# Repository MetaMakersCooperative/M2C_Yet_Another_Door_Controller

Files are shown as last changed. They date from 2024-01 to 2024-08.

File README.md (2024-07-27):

# M2C Yet Another Door Controller

Proof of concept for new door controller design using a `WT32-ETH01`.

## Development Requirements

Make sure version `v1.X` of the Arduino IDE installed. It is required to upload the cards file. See [Cards File](#cards_file) section.

`arduino-cli` also needs to be installed to compile and upload the sketch. It is possible to use the Arduino IDE `v1.X` or `v2` but they have not been tested/verified. Milage may vary.

## Cards File

The sketch assumes a file named `cards.txt` exists within a `LitteFS` file system. The code will not function correctly without it.

Unfortunately, the only way to upload the file to the device is using `v1.X` Arduino IDE. This is because the upload using a plugin that only can be used with that version of the IDE. Setting up the upload plugin is only required if the `cards.txt` file needs to be updated or if the flash storage was wiped.

### Setup the Upload Plugin

To setup the plugin, follow the steps outlined below:

1. First download the following `zip` file: [https://github.com/lorol/arduino-esp32fs-plugin/releases/download/2.0.7/esp32fs.zip](https://github.com/lorol/arduino-esp32fs-plugin/releases/download/2.0.7/esp32fs.zip)
2. Unzip and place the `esp32fs.jar` file in the following directory: `~/Arduino/tools/ESP32FS/tool/esp32fs.jar`
3. Restart Arduino IDE if it's running

### Uploading

Before uploading, create the `data` directory in the project root if it does not already exist. Update/create the `card.txt` file with the codes that should unlock the door. Make sure each code is in it's own line, like below:

> Each code should be no more than 10 digits long and only container digits `0-9`. No leading zeros!

```text
1234567
8912345
6789123
```

Double check and make sure the project structure matches the following:

```text
~/Arduino/M2C_Yet_Another_Door_Controller/
├── data
│   └── cards.txt
├── README.md
├── sketch.yaml
└── M2C_Yet_Another_Door_Controller.ino
```

To upload the `card.txt` file, follow the steps outlined below:

> When referencing the Arduino IDE, it is implied that it's `v1.X` not `v2`

1. Open Arduino IDE and open the `M2CYetAnotherDoorController.ino` sketch.
2. Navigate and click on `Tools -> Board` and select `WT32-ETH01 Ethernet Module` if it is not already selected.
3. Navigate and click on `Tools -> ESP32 Sketch Date Upload`
4. Select `LittleFS` then click `OK`

## Libraries

To install the `esp32` libraries run the following command:

```bash
arduino-cli core install esp32:esp32@3.0.2
```

> Might need to run `arduino-cli core update-index` to update the board index.

This will install [espressif/arduino-esp32 version `3.0.2`](https://github.com/espressif/arduino-esp32/tree/3.0.2).

The following libraries can be installed using the Arduino IDE or by downloading the files directly from the source repositories.

When downloading the libraries manually, make sure the source is place them within the following directory: `~/Arduino/libraries`.

The `libraries` should look like this assuming the only installed libraries are the ones used by this project.

```
~/Arduino/libraries
├── LinkedList
│   ├── ...
└── Yet_Another_Arduino_Wiegand_Library
    ├── ...
```

> Make sure to download the source tagged with the versions listed below!

The following dependencies need to be installed manually as the latest versions are required:

> The best way to get these libraries is to `git clone` them into the `~/Arduino/libraries` directory.

- [Yet Another Arduino Wiegand Library](https://github.com/paulo-raca/YetAnotherArduinoWiegandLibrary) commit: `556e7b8` tag: `2.0.1`
- [LinkedList](https://github.com/ivanseidel/LinkedList) commit: `0439a72` tag: `v1.3.3`
- [espMqttClient](https://github.com/bertmelis/espMqttClient) commit: `70d3113` tag: `v1.7.0`
- [AsyncTCP](https://github.com/mathieucarbou/AsyncTCP) commit: `b20e92e` tag: `v3.1.4`

> AsyncTCP is still required even though it's not being used

## Commands (using CLI)

> Note: `/dev/ttyUSB0` is the default device. Run the following command to see what device is being used: `arduino-cli board list`. Make sure to modify the commands below to match that device.

To compile the sketch with defaults, run following command:

> WARNING: Defaults will apply not overridden which could cause a lot of problems on multi door deployments. See the [Override Defaults](#override-defaults) section below.

```bash
arduino-cli compile --fqbn esp32:esp32:wt32-eth01 ./
```

To enable more debugging messages, run the following command:

```bash
arduino-cli compile --build-property "build.extra_flags=\"-DDC_DEBUG=1\"" --clean --fqbn esp32:esp32:wt32-eth01 ./
```

To Upload the compiled sketch:

```bash
arduino-cli upload -p /dev/ttyUSB0 --fqbn esp32:esp32:wt32-eth01 ./
```

To monitor the serial output:

```bash
arduino-cli monitor --log-level debug --fqbn esp32:esp32:wt32-eth01 -p /dev/ttyUSB0 -c baudrate=115200
```
## MQTT Broker

> NOTE: The code assumes the MQTT server connection is TLS. Only TLS v1.2 is supported. Using TLS v1.3 will result in some weird errors. 

The device will send logs, lock, unlock, and other events to the configured MQTT broker. If disconnected, only a few messages will be queued and sent when it's able to reconnect.

If the `door_controller/access_list` topic is received, the device will replace the card file with the payload, then attempt to reload the list from the updated file.

The device will also respond to messages with the `door_controller/health_check` topic. This is designed to help with monitoring the healthiness of the device.

### `root_ca.h`

Use the example file, `root_ca.h.example`, to create the `root_ca.h` file containing the root certificate for the MQTT broker.

> NOTE: The root certificate will expire at some point so make sure you mark it in your calendar!

If you're using Let's Encrypt, then there is a good chance that the root certificate can be download from the following URL: [letsencrypt.org/certs/isrgrootx1.pem](https://letsencrypt.org/certs/isrgrootx1.pem)

Otherwise, check out [letsencrypt.org/certificates/](https://letsencrypt.org/certificates/) for a complete list.

## Override Defaults

> Note: Make sure the latest Arduino CLI is installed

The table below shows the build flags that should be overridden for each controller being deployed.
Refer to the source files for a complete list of overridable flags.

| Flag Name | Default | Description | Build Argument |
|---|---|---|---|
| DC_HOST_NAME | m2cdoorone | The value that will be set as the device's host name | -DDC_HOST_NAME=m2cdoorone |
| DC_CLIENT_ID | door_one | Client ID is used by the MQTT broker to identify the client. This value needs to be unique across all clients connected to the broker | -DDC_CLIENT_ID=door_one |
| DC_MQTT_HOST | mqtt.metamakers.org | Host name for the MQTT Broker. The host name is used to get the server IP using DNS | -DDC_MQTT_HOST=mqtt.metamakers.org |
| DC_MQTT_USER | door_one | The user that the MQTT client will use to authenticate | -DDC_MQTT_USER=door_one |
| DC_MQTT_PW | Door_One!1 | The password that the MQTT client will use to authenticate | -DDC_MQTT_PW=Door_One!1 |
| DC_NTP_HOST  | pool.ntp.org | The domain used to update the RTC using NTP | -DDC_NTP_HOST=pool.ntp.org |
| DC_DEBUG | 0 | Enable more verbose debugging information via the serial port. Do not enable this for production deployments | -DDC_DEBUG=0 |

Below is an example of how to override all the flags in the table above:

> Documentation on the CLI compile command can be found [here](https://arduino.github.io/arduino-cli/1.0/commands/arduino-cli_compile/).

```bash
arduino-cli compile --build-property "build.extra_flags=-DDC_DEBUG=0 \"-DDC_HOST_NAME=\"m2cdoorone\"\" \"-DDC_CLIENT_ID=\"door_one\"\" \"-DDC_MQTT_HOST=\"mqtt.metamakers.org\"\" \"-DDC_MQTT_USER=\"door_one\"\" \"-DDC_MQTT_PW=\"Door_One!1\"\" \"-DDC_NTP_HOST=\"pool.ntp.org\"\"" --clean --fqbn esp32:esp32:wt32-eth01 ./
```

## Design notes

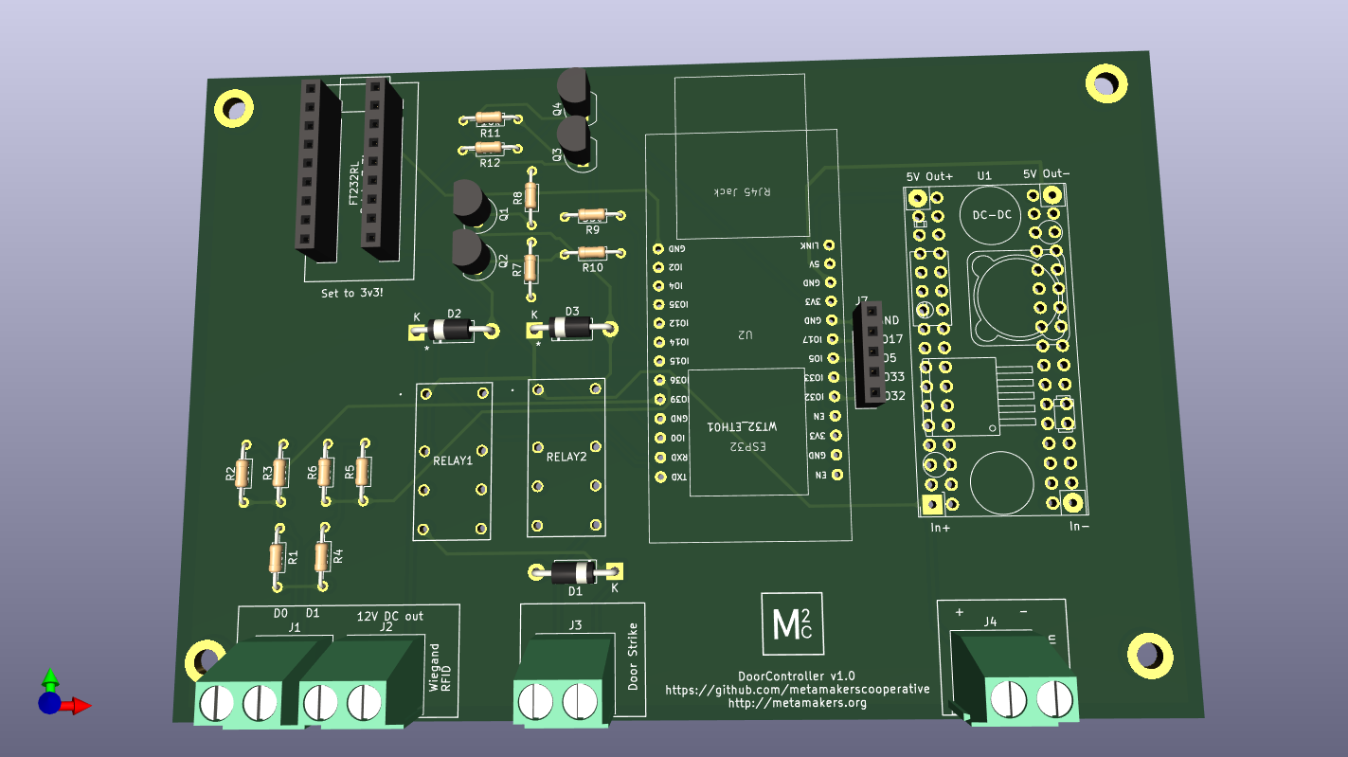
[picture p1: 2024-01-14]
PCB/door-controller.png

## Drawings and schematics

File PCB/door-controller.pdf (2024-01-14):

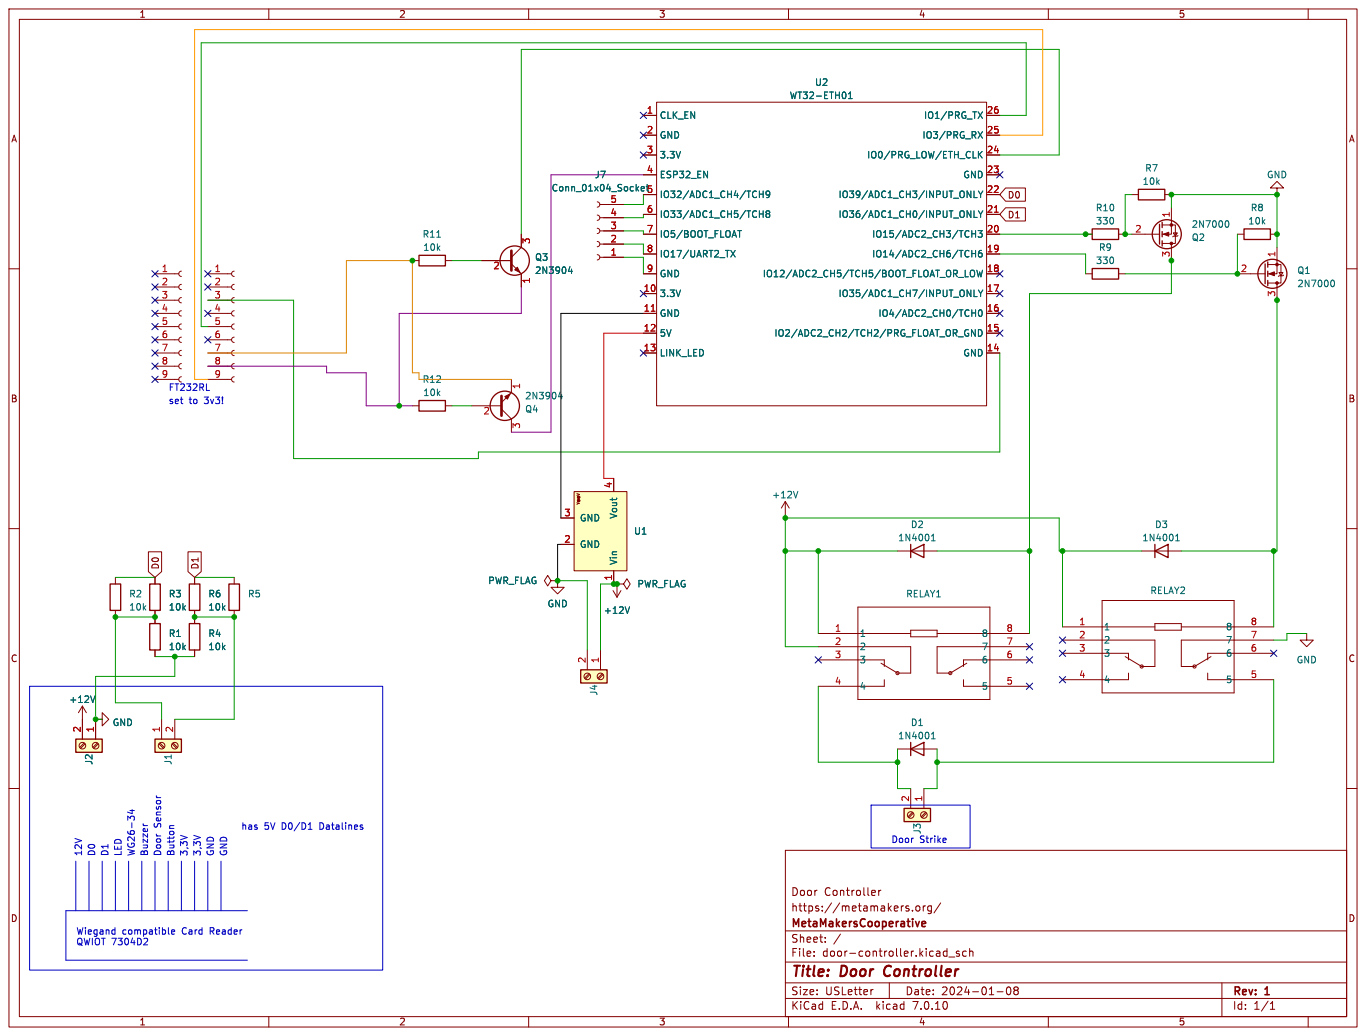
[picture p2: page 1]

1 GND 2 GND 3 Vout 4 U1
https://metamakers.org/ Door Controller 1

Id: 1/1 Title: Door Controller File: door-controller.kicad_sch Sheet: / MetaMakersCooperative

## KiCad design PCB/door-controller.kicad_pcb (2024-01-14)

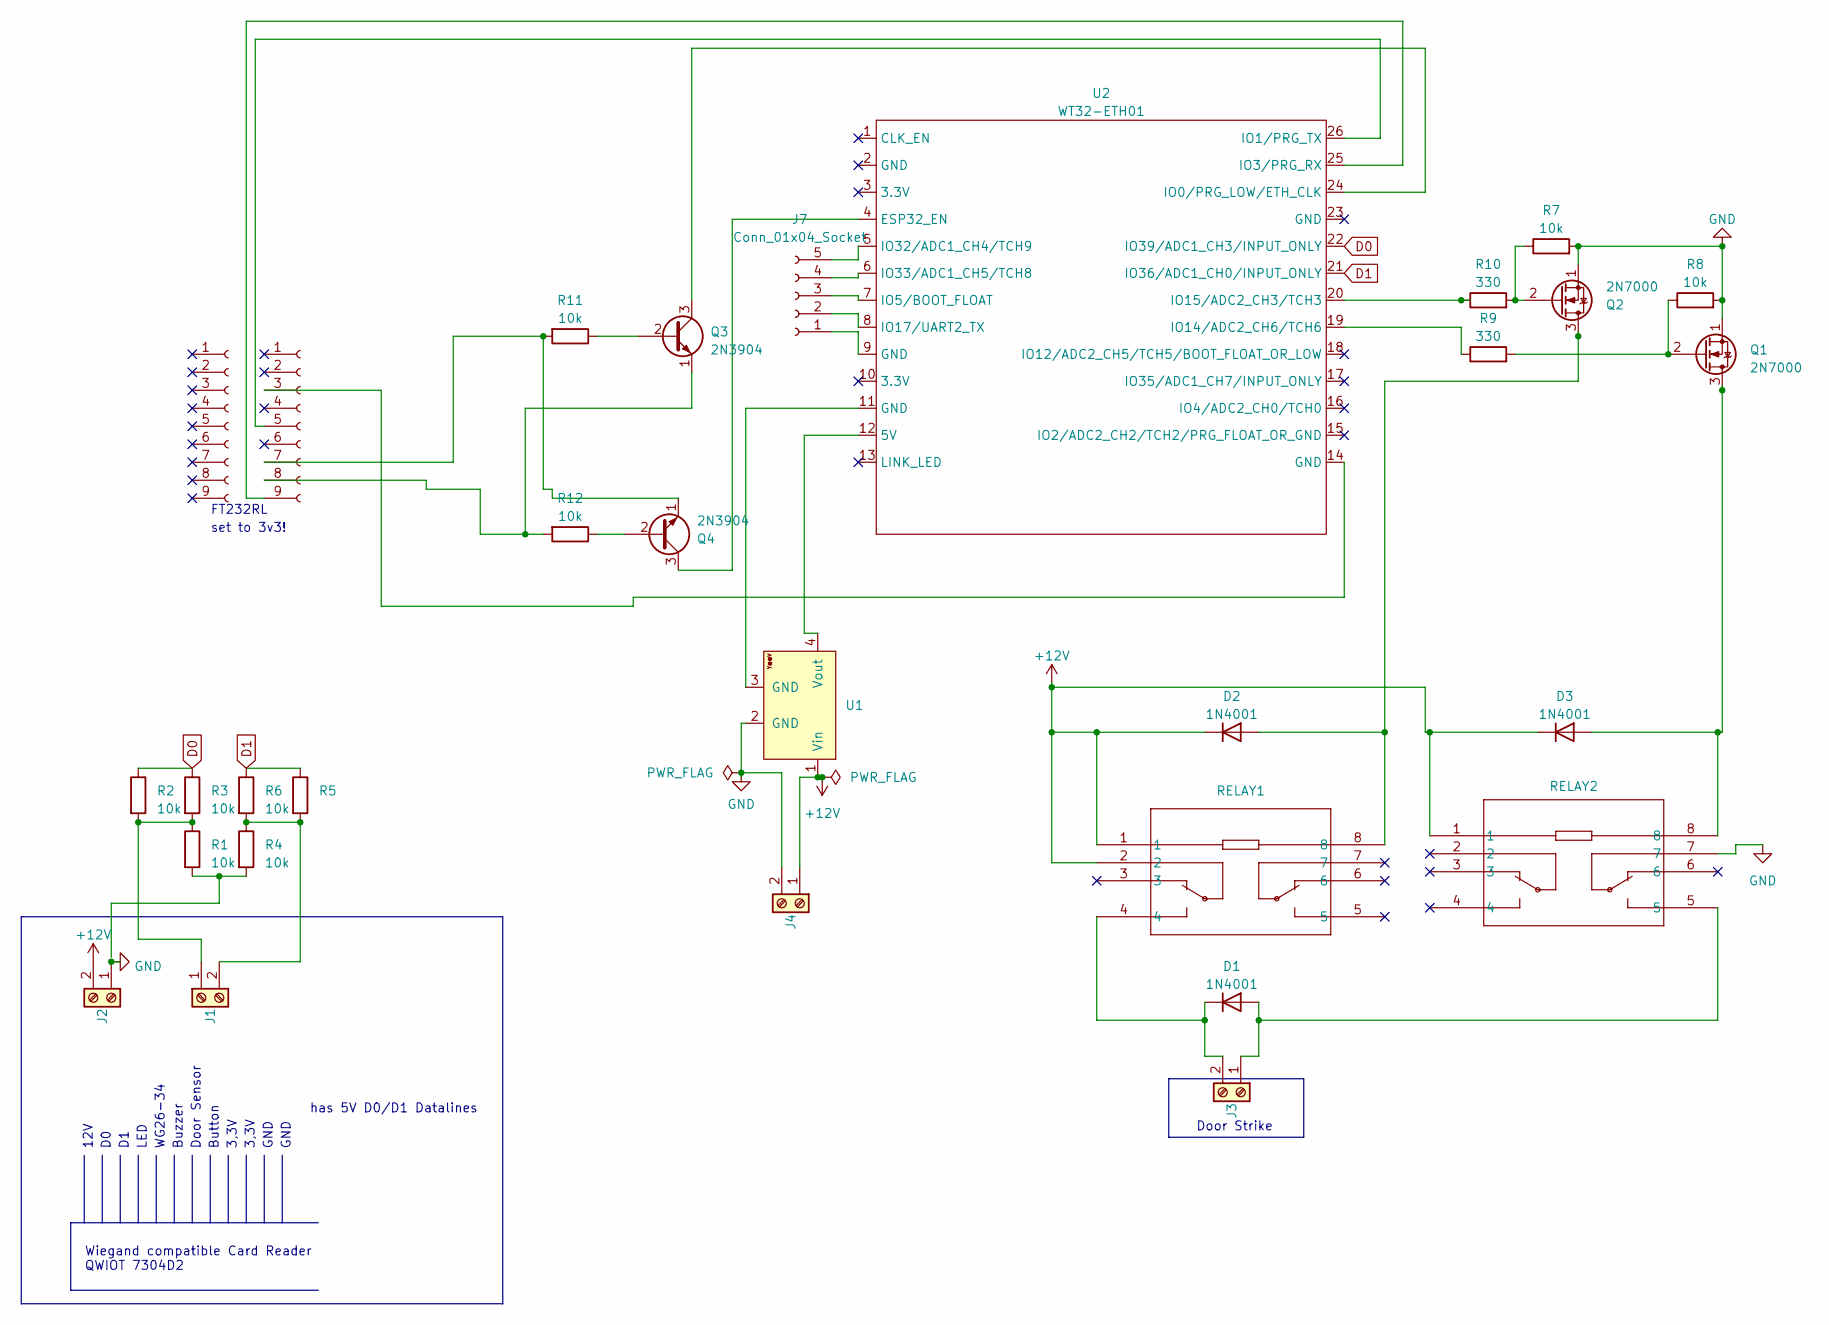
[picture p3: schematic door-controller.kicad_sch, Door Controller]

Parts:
D1, D2, D3: 1N4001; D_DO-41_SOD81_P10.16mm_Horizontal
J1, J2, J3, J4: TerminalBlock_Phoenix_MKDS-1,5-2_1x02_P5.00mm_Horizontal
J5, J6: Conn_01x09_Socket; PinSocket_1x09_P2.54mm_Vertical
J7: Conn_01x04_Socket; PinSocket_1x05_P2.54mm_Vertical
Q1, Q2: 2N7000; TO-92_Inline
Q3, Q4: 2N3904; TO-92_Inline
R1, R2, R3, R4, R5, R6, R7, R8, R11, R12: 10k; R_Axial_DIN0204_L3.6mm_D1.6mm_P7.62mm_Horizontal
R9, R10: 330; R_Axial_DIN0204_L3.6mm_D1.6mm_P7.62mm_Horizontal
RELAY1, RELAY2: RELAY8_J104D2C12VDC.20S_CRS
U1: YAAJ_DCDC_StepDown_LM2596; YAAJ_DCDC_StepDown_LM2596_Universal
U2: WT32-ETH01

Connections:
+12V: D2.1 (K), D3.1 (K), J2.2, J4.1, RELAY1.1, RELAY1.2, RELAY2.1, U1.1 (Vin)
D0: R2.1, R3.1, U2.22 (IO39/ADC1_CH3/INPUT_ONLY)
D1: R5.1, R6.1, U2.21 (IO36/ADC1_CH0/INPUT_ONLY)
GND: J2.1, J4.2, Q1.1 (S), Q2.1 (S), R7.2, R8.2, RELAY2.7, U1.2 (GND)
unnamed: D1.2 (A), J3.1, RELAY2.5
unnamed: D1.1 (K), J3.2, RELAY1.4
unnamed: D2.2 (A), Q2.3 (D), RELAY1.8
unnamed: D3.2 (A), Q1.3 (D), RELAY2.8
unnamed: J1.1, R1.1, R2.2, R3.2
unnamed: J1.2, R4.1, R5.2, R6.2
unnamed: J6.3, U2.14 (GND)
unnamed: J6.5, U2.26 (IO1/PRG_TX)
unnamed: J6.7, Q4.1 (E), R11.2
unnamed: J6.8, Q3.1 (E), R12.2
unnamed: J6.9, U2.25 (IO3/PRG_RX)
unnamed: J7.1, U2.9 (GND)
unnamed: J7.2, U2.8 (IO17/UART2_TX)
unnamed: J7.3, U2.7 (IO5/BOOT_FLOAT)
unnamed: J7.4, U2.6 (IO33/ADC1_CH5/TCH8)
unnamed: J7.5, U2.5 (IO32/ADC1_CH4/TCH9)
unnamed: Q1.2 (G), R8.1, R9.2
unnamed: Q2.2 (G), R7.1, R10.2
unnamed: Q3.2 (B), R11.1
unnamed: Q3.3 (C), U2.24 (IO0/PRG_LOW/ETH_CLK)
unnamed: Q4.2 (B), R12.1
unnamed: Q4.3 (C), U2.4 (ESP32_EN)
unnamed: R1.2, R4.2
unnamed: U1.3 (GND), U2.11 (GND)
unnamed: U1.4 (Vout), U2.12 (5V)
unnamed: R9.1, U2.19 (IO14/ADC2_CH6/TCH6)
unnamed: R10.1, U2.20 (IO15/ADC2_CH3/TCH3)

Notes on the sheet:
12V
3,3V
Door Strike
Buzzer
WG26-34
Button
GND
FT232RL
has 5V D0/D1 Datalines
Wiegand compatible Card Reader QWIOT 7304D2
Door Sensor
LED
GND
set to 3v3!

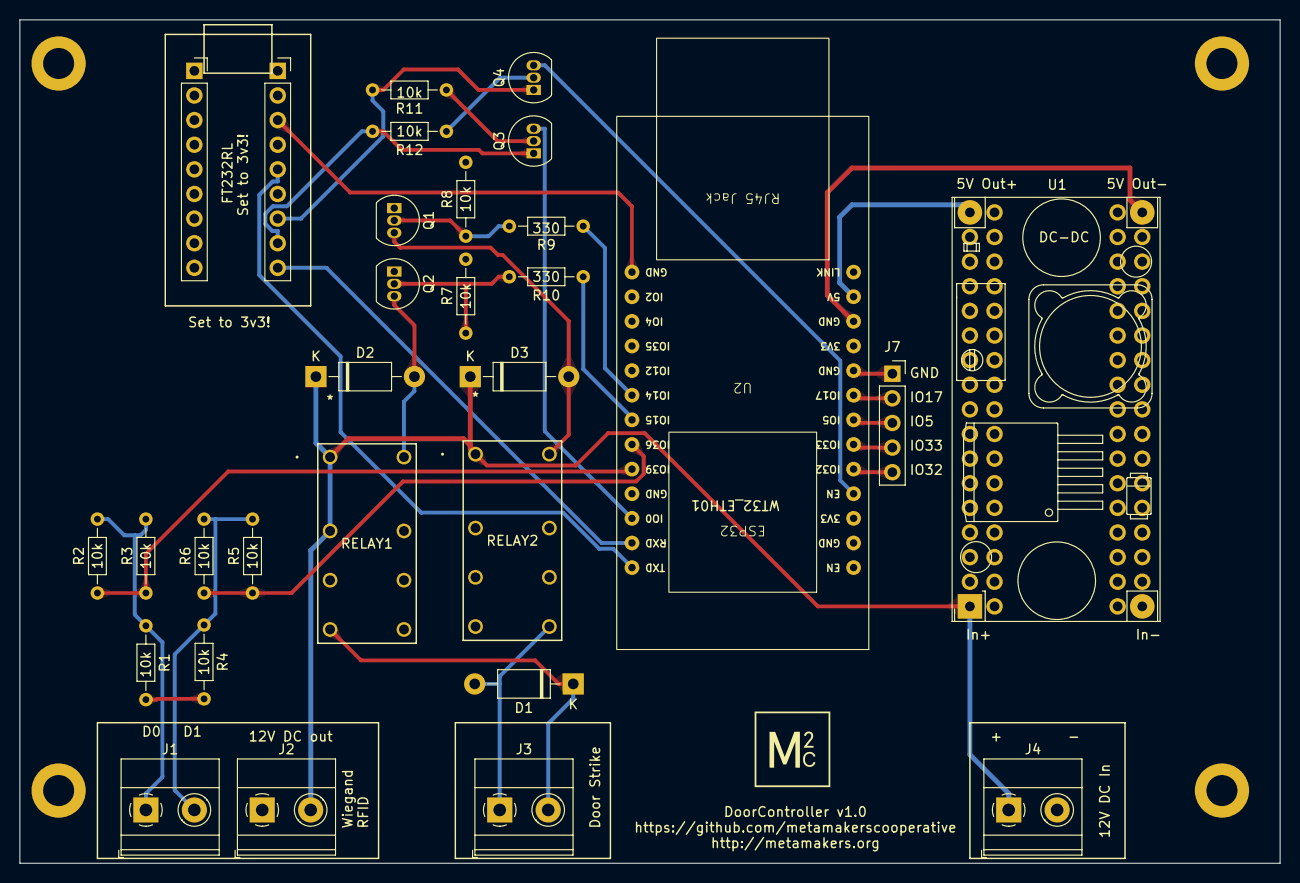
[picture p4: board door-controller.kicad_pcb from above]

Board: 2 copper layers, 130.0 x 87.0 mm, 34 parts (0 on the bottom side), 31 nets.

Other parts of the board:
MH1, MH2, MH3, MH4: MountingHole_3.2mm_M3_DIN965_Pad

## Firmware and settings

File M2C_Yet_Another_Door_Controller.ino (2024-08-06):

#include <Wiegand.h>
#include <LittleFS.h>
#include <LinkedList.h>
#include <errno.h>
// Dependencies: freertos/FreeRTOS.h and AsyncTCP.h
#include <espMqttClient.h>

// Note: These need to be defined BEFORE including ETH.h or calling ETH.begin()
#ifndef ETH_PHY_TYPE
#define ETH_PHY_TYPE ETH_PHY_LAN8720
#define ETH_PHY_ADDR 0
#define ETH_PHY_MDC 23
#define ETH_PHY_MDIO 18
#define ETH_PHY_POWER -1
#define ETH_CLK_MODE ETH_CLOCK_GPIO0_IN
#endif

#include <ETH.h>

#include "root_ca.h"

// The value that will be set as the device's host name
#ifndef DC_HOST_NAME
#define DC_HOST_NAME "m2cdoorone"
#endif

// Client ID is used by the MQTT broker to identify the client
// This value needs to be unique across all clients connected to the broker
#ifndef DC_CLIENT_ID
#define DC_CLIENT_ID "door_one"
#endif

// Host name for the MQTT Broker. The host name is used to get the server IP using DNS
#ifndef DC_MQTT_HOST
#define DC_MQTT_HOST "mqtt.metamakers.org"
#endif

// The user that the MQTT client will use to authenticate
#ifndef DC_MQTT_USER
#define DC_MQTT_USER "door_one"
#endif

// The password that the MQTT client will use to authenticate
#ifndef DC_MQTT_PW
#define DC_MQTT_PW "Door_One!1"
#endif

// The domain used to update the RTC using NTP
#ifndef DC_NTP_HOST
#define DC_NTP_HOST "pool.ntp.org"
#endif

// Enable more verbose debugging information via the serial port
// Do not enable this for production deployments
#ifndef DC_DEBUG
#define DC_DEBUG 0
#endif

// How long the client should wait before trying to reconnect to the MQTT Broker
#define DC_MQTT_RECONNECT_DELAY 20000

// How long to wait to refresh the RTC using NTP
// Default is set to 1 day
#define DC_NTP_REFRESH_TIME 86400000

// Publish MQTT topics with the client ID as the last level
#define TOPIC_LOG_INFO "door_controller/log_info/" DC_CLIENT_ID
#define TOPIC_LOG_WARN "door_controller/log_warn/" DC_CLIENT_ID
#define TOPIC_LOG_FATAL "door_controller/log_fatal/" DC_CLIENT_ID
#define TOPIC_UNLOCK "door_controller/unlock/" DC_CLIENT_ID
#define TOPIC_LOCK "door_controller/lock/" DC_CLIENT_ID
#define TOPIC_DENIED_ACCESS "door_controller/denied_access/" DC_CLIENT_ID
#define TOPIC_CHECK_IN "door_controller/check_in/" DC_CLIENT_ID

// Subscribe MQTT topics
#define TOPIC_ACCESS_LIST "door_controller/access_list"
#define TOPIC_HEALTH_CHECK "door_controller/health_check"

// These are the pins connected to the Wiegand D0 and D1 signals.
// Ensure your board supports external Interruptions on these pins
#define PIN_D0 39
#define PIN_D1 36

// Change this value to increase/decrease the amount of time the
// door is unlocked
#define UNLOCK_DOOR_MS 8000

// Relay pins to (un)lock the door
#define PIN_IO14 15
#define PIN_IO15 14

// Possible door states
#define STATE_NORMAL 0
#define STATE_UNLOCKED 1
#define STATE_COMPARING 2
#define STATE_MATCH 3

struct DoorState {
    uint8_t state;
    uint32_t cardCode;
    long doorUnlockedAtMS;
    int cursor;
};

espMqttClientSecure mqttClient(espMqttClientTypes::UseInternalTask::NO);
static TaskHandle_t taskHandle;

long lastReconnectAttempt = 0;

LinkedList<uint32_t> codeList = LinkedList<uint32_t>();

Wiegand wiegand;

DoorState doorState;

IPAddress mqttServerIp;
bool hasIp = false;

long lastNTPRefresh = 0;

void setup() {
    Serial.begin(115200);
    Serial.println("Listening...");

    if (DC_DEBUG == 1) {
        Serial.println("Echo flags for debugging");
        Serial.print("DC_HOST_NAME: ");
        Serial.print(DC_HOST_NAME);
        Serial.print(", DC_CLIENT_ID: ");
        Serial.print(DC_CLIENT_ID);
        Serial.print(", DC_MQTT_HOST: ");
        Serial.print(DC_MQTT_HOST);
        Serial.print(", DC_MQTT_USER: ");
        Serial.print(DC_MQTT_USER);
        Serial.print(", DC_MQTT_PW: ");
        Serial.print(DC_MQTT_PW);
        Serial.println("");
    }

    // NOTE: mqttClient needs to be configured BEFORE the ETH.begin() call.
    // In the event that the board is restarted, the ETH connected event will
    // trigger almost immediately. When the event is triggered the mqttClient
    // is set to attempt to connect. If the below lines haven't been called yet
    // then the mqttClient will attempt to connect with the wrong config.
    mqttClient.setClientId(DC_CLIENT_ID);
    mqttClient.setCredentials(DC_MQTT_USER, DC_MQTT_PW);
    mqttClient.setCACert(root_ca);
    mqttClient.onDisconnect(onMqttDisconnect);
    mqttClient.onConnect(onMqttConnect);
    mqttClient.onMessage(onMqttMessage);
    mqttClient.setTimeout(5);
    mqttClient.setKeepAlive(15);

    xTaskCreatePinnedToCore(
        (TaskFunction_t)networkingTask,
        "mqttclienttask",
        5120,
        nullptr,
        1,
        &taskHandle,
        0
    );

    // ETH/Network code inspired by:
    // https://github.com/espressif/arduino-esp32/blob/3.0.2/libraries/Ethernet/examples/ETH_TLK110/ETH_TLK110.ino
    Network.onEvent(networkEvent);
    ETH.begin(
        ETH_PHY_TYPE,
        ETH_PHY_ADDR,
        ETH_PHY_MDC,
        ETH_PHY_MDIO,
        ETH_PHY_POWER,
        ETH_CLK_MODE
    );

    if (DC_DEBUG == 1) {
        Serial.print("DNS IP: ");
        Serial.print(ETH.dnsIP());
        Serial.println();
    }
    mqttClient.publish(TOPIC_LOG_INFO, 1, false, "Starting setup");

    doorState = {STATE_NORMAL, 0, 0, 0};

    if (!LittleFS.begin()) {
        Serial.println("An Error has occurred while mounting LittleFS");
        mqttClient.publish(TOPIC_LOG_FATAL, 1, false, "Failed to mount file system.");
        return;
    }

    File file = LittleFS.open("/cards.txt", FILE_READ);
    if (!file) {
        Serial.println("Failed to open file for reading");
        mqttClient.publish(TOPIC_LOG_FATAL, 1, false, "Failed to open cards.txt");
        return;
    } else {
        buildCodeList(file);
        file.close();
    }

    char listSize[31];
    sprintf(listSize, "Code list size: %d", codeList.size());
    mqttClient.publish(TOPIC_LOG_INFO, 1, false, listSize);
    Serial.println(listSize);
    if (codeList.size() == 0) {
        Serial.println("Code list is empty! cards.txt is likely malformed or corrupted!");
        mqttClient.publish(
            TOPIC_LOG_WARN,
            1,
            false,
            "Code list is empty! cards.txt is likely malformed or corrupted!"
        );
    }

    mqttClient.publish(TOPIC_LOG_INFO, 1, false, "Configuring wiegand");
    wiegand.onReceive(receiveCardCode, &doorState);
    wiegand.onReceiveError(receivedDataError, "Card read error: ");
    wiegand.onStateChange(stateChanged, "State changed: ");
    wiegand.begin(Wiegand::LENGTH_ANY, true);
    mqttClient.publish(TOPIC_LOG_INFO, 1, false, "wiegand configured");

    pinMode(PIN_D0, INPUT);
    pinMode(PIN_D1, INPUT);
    pinMode(PIN_IO14, OUTPUT);
    pinMode(PIN_IO15, OUTPUT);
    digitalWrite(PIN_IO14, LOW);
    digitalWrite(PIN_IO15, LOW);
    attachInterrupt(digitalPinToInterrupt(PIN_D0), pinStateChanged, CHANGE);
    attachInterrupt(digitalPinToInterrupt(PIN_D1), pinStateChanged, CHANGE);

    pinStateChanged();
    mqttClient.publish(TOPIC_LOG_INFO, 1, false, "Setup complete");
}

void loop() {
    char payload[31];
    switch (doorState.state) {
        case STATE_NORMAL: 
            break;
        case STATE_UNLOCKED:
            if ((millis() - doorState.doorUnlockedAtMS) >= UNLOCK_DOOR_MS) {
                digitalWrite(PIN_IO14, LOW);
                digitalWrite(PIN_IO15, LOW);
                createCardAndTimePayload(payload);
                Serial.println("Locking door.");
                mqttClient.publish(TOPIC_LOCK, 1, false, payload);

                doorState.doorUnlockedAtMS = 0;
                doorState.cardCode = 0;
                doorState.state = STATE_NORMAL;
            }
            break;
        case STATE_MATCH:
            digitalWrite(PIN_IO14, HIGH);
            digitalWrite(PIN_IO15, HIGH);

            createCardAndTimePayload(payload);
            Serial.print("Unlocking door for: ");
            Serial.println(payload);
            mqttClient.publish(TOPIC_UNLOCK, 1, false, payload);

            Serial.println("Unlocking door ...");
            doorState.doorUnlockedAtMS = millis();
            doorState.state = STATE_UNLOCKED;
            doorState.cursor = 0;
            break;
        case STATE_COMPARING:
            if (doorState.cursor >= codeList.size()) {
                createCardAndTimePayload(payload);
                Serial.print("Denied access: ");
                Serial.println(payload);
                mqttClient.publish(TOPIC_DENIED_ACCESS, 1, false, payload);
                doorState.state = STATE_NORMAL;
                doorState.cursor = 0;
                doorState.cardCode = 0;
                break;
            }
            uint32_t testCode = codeList.get(doorState.cursor);
            if (doorState.cardCode == testCode) {
                Serial.println("Match!!");
                doorState.state = STATE_MATCH;
                break;
            }
            doorState.cursor += 1;
            break;
    }

    if (doorState.state != STATE_COMPARING) {
        Serial.flush();
        noInterrupts();
        wiegand.flush();
        interrupts();

        if (attemptMqttConnection() && millis() - lastReconnectAttempt > DC_MQTT_RECONNECT_DELAY) {
            connectToMqtt();
        }

        if (ETH.linkUp() && hasIp) {
            if (millis() - lastNTPRefresh > DC_NTP_REFRESH_TIME) {
                xTaskCreate(setClock, "set_clock", 10000, NULL, 1, NULL);
                lastNTPRefresh = millis();
            }
        }
        delay(100);
    }
}

void networkingTask() {
  for (;;) {
    mqttClient.loop();
  }
}

void buildCodeList(File &file) {
    mqttClient.publish(TOPIC_LOG_INFO, 1, false, "Building code list");
    Serial.println("Building List");

    char digits[11];
    int digitCursor = 0;
    while (file.available()) {
        digits[0] = '\0';
        digitCursor = 0;

        int character;
        while (digitCursor < 10) {
            character = file.read();
            if (character == '\n' || character == EOF) break;
            digits[digitCursor] = character;
            digitCursor += 1;
        }

        digits[digitCursor] = '\0';
        if (digitCursor == 0) {
            Serial.println("No data found between line \\n characters.");
            mqttClient.publish(TOPIC_LOG_WARN, 1, false, "No data found between line \\n characters.");
            continue;
        }

        // If the digitCursor is 10, then 10 characters were read from the file.
        // Need to read the next
        if (digitCursor == 10) {
            character = file.read();
        }

        if (DC_DEBUG == 1) {
            Serial.printf("Char as number: %d", character);
            Serial.println();
            Serial.printf("last character: %#x", character);
            Serial.println();
            Serial.print("First 10 bytes: ");
            char *idx = digits;
            while(idx < digits + 10) {
                if (*idx == '\0' || *idx == EOF) break;
                Serial.printf(" %#x ", *idx);
                idx += 1;
            }
            Serial.println();
            Serial.printf("Digits: %s", digits);
            Serial.println();
            Serial.printf("Digits read: %d", digitCursor);
            Serial.println();
            Serial.flush();
        }

        // If there are more characters than the expected 10 then it's not
        // safe to assume that the characters read are a code that should
        // be able to unlock the door.
        if (character != '\n' && character != EOF) {
            Serial.println("Found more characters than expected. Ignoring.");
            while (character != '\n' && character != EOF) {
                character = file.read();
            }
            continue;
        }

        char *endPointer = 0;
        uint32_t code = strtoul(digits, &endPointer, 10);
        if ((errno == ERANGE && code == UINT32_MAX) || (errno != 0 && code == 0)) {
            Serial.print("Conversion error occurred with: ");
            Serial.println(digits);
            Serial.println("Skipping entry.");
            continue;
        }
        if (strcmp(endPointer, digits) == 0) {
            Serial.println("No digits were found. Ignoring.");
            continue;
        }
        codeList.add(code);
    }
}

void createCardAndTimePayload(char *payload) {
    struct tm timeinfo;
    bool hasTime = true;

    if(!getLocalTime(&timeinfo)){
        Serial.println("Failed to obtain time");
        mqttClient.publish(TOPIC_LOG_WARN, 1, false, "Failed to get time from RTC");
        hasTime = false;
    }

    sprintf(payload, "%010d", doorState.cardCode);

    if (hasTime) {
        char time[21];
        strftime(time, 21, "|%F %T", &timeinfo);
        strcat(payload, time);
    }
}

bool attemptMqttConnection() {
    return mqttClient.disconnected() && ETH.linkUp() && hasIp;
}

void connectToMqtt() {
    Serial.println("MQTT connecting ...");
    if (ETH.linkUp() && hasIp) {
        lastReconnectAttempt = millis();
        mqttClient.connect();
    } else {
        Serial.println("Cannot create connection to MQTT. Ethernet is down.");
        Serial.print("ETH Link Status: ");
        Serial.println(ETH.linkUp());
        Serial.print("ETH IP: ");
        Serial.println(ETH.localIP());
        Serial.flush();
    }
}

void onMqttConnect(bool sessionPresent) {
    Serial.println("Connected to MQTT.");
    mqttClient.subscribe(TOPIC_ACCESS_LIST, 1);
    mqttClient.subscribe(TOPIC_HEALTH_CHECK, 1);
}

void onMqttDisconnect(espMqttClientTypes::DisconnectReason reason) {
    Serial.print("MQTT Disconnected - Code: ");
    Serial.print(static_cast<uint8_t>(reason));
    Serial.print(" - Reason: ");
    switch (reason) {
        case espMqttClientTypes::DisconnectReason::TCP_DISCONNECTED:
            Serial.println("TCP disconnected");
            break;
        case espMqttClientTypes::DisconnectReason::MQTT_NOT_AUTHORIZED:
            Serial.println("Not Authorized");
            break;
        case espMqttClientTypes::DisconnectReason::MQTT_SERVER_UNAVAILABLE:
            Serial.println("Server unavailabled");
            break;
        case espMqttClientTypes::DisconnectReason::MQTT_MALFORMED_CREDENTIALS:
            Serial.println("Malformed credentials");
            break;
        case espMqttClientTypes::DisconnectReason::MQTT_IDENTIFIER_REJECTED:
            Serial.println("Identifier rejected");
            break;
        case espMqttClientTypes::DisconnectReason::MQTT_UNACCEPTABLE_PROTOCOL_VERSION:
            Serial.println("Unacceptable protocol version");
            break;
        case espMqttClientTypes::DisconnectReason::TLS_BAD_FINGERPRINT:
            Serial.println("TLS bad fingerprint");
            break;
        case espMqttClientTypes::DisconnectReason::USER_OK:
            Serial.println("User ok");
            break;
        default:
            Serial.println("Unknown");
            break;
    }
}

void onMqttMessage(
    const espMqttClientTypes::MessageProperties& properties,
    const char* topic,
    const uint8_t* payload,
    size_t len,
    size_t index,
    size_t total
) {
    if (DC_DEBUG == 1) {
        Serial.println("Publish received.");
        Serial.print("  topic: ");
        Serial.println(topic);
        Serial.print("  qos: ");
        Serial.println(properties.qos);
        Serial.print("  dup: ");
        Serial.println(properties.dup);
        Serial.print("  retain: ");
        Serial.println(properties.retain);
        Serial.print("  len: ");
        Serial.println(len);
        Serial.print("  index: ");
        Serial.println(index);
        Serial.print("  total: ");
        Serial.println(total);
    }
    char infoPayload[300];
    snprintf(
        infoPayload,
        300,
        "P:%s|QOS:%u|DUP:%d|R:%d|L:%u|I:%u|T:%u",
        topic,
        properties.qos,
        properties.dup,
        properties.retain,
        len,
        index,
        total
    );

    mqttClient.publish(TOPIC_LOG_INFO, 1, false, infoPayload);
    if (index != 0 || (len < total)) {
        mqttClient.publish(TOPIC_LOG_WARN, 1, false, "Split payload, ignoring");
        return;
    } else if (properties.dup) {
        mqttClient.publish(TOPIC_LOG_WARN, 1, false, "Received duplicate, ignoring");
        return;
    } else if (strcmp(topic, TOPIC_ACCESS_LIST) == 0) {
        File file = LittleFS.open("/cards.txt", FILE_WRITE);
        if (!file) {
            Serial.println("Failed to open cards.txt for writing");
            mqttClient.publish(TOPIC_LOG_FATAL, 1, false, "Failed to open cards.txt for writing");
            return;
        }

        Serial.println("Rebuilding cards.txt");
        mqttClient.publish(TOPIC_LOG_INFO, 1, false, "Rebuilding cards.txt");

        int payloadCursor = 0;
        while (payloadCursor < len) {
            char value = *(payload + payloadCursor);
            file.write(value);
            payloadCursor += 1;
        }
        file.flush();
        file.close();

        file = LittleFS.open("/cards.txt", FILE_READ);
        if (!file) {
            Serial.println("Failed to read cards.txt");
            mqttClient.publish(TOPIC_LOG_FATAL, 1, false, "Failed to read cards.txt");
            return;
        }

        codeList.clear();
        buildCodeList(file);
        file.close();

        Serial.println("Completed rebuilding cards.txt");
        mqttClient.publish(TOPIC_LOG_INFO, 1, false, "Completed rebuilding cards.txt");

    } else if (strcmp(topic, TOPIC_HEALTH_CHECK) == 0) {
        Serial.println("Received health check message");
        mqttClient.publish(TOPIC_CHECK_IN, 1, false, DC_CLIENT_ID);
    } else {
        char payload[100];
        snprintf(payload, 100, "%s", "Recieved an unknown topic:  %s", topic);
        mqttClient.publish(TOPIC_LOG_INFO, 1, false, payload);
        Serial.println(payload);
    }
}

// When any of the pins have changed, update the state of the wiegand library
void pinStateChanged() {
    wiegand.setPin0State(digitalRead(PIN_D0));
    wiegand.setPin1State(digitalRead(PIN_D1));
}

// Notifies when a reader has been connected or disconnected.
// Instead of a message, the seconds parameter can be anything you want -- Whatever you specify on `wiegand.onStateChange()`
void stateChanged(bool plugged, const char* message) {
    char payload[100];
    if (plugged) {
        snprintf(payload, 100, "%s", "Wiegand disconnected: %s", message);
        mqttClient.publish(TOPIC_LOG_INFO, 1, false, payload);
        Serial.println(payload);
    } else {
        snprintf(payload, 100, "%s", "Wiegand disconnected: %s", message);
        mqttClient.publish(TOPIC_LOG_INFO, 1, false, payload);
        Serial.println(payload);
    }
}

void receiveCardCode(uint8_t* data, uint8_t bits, DoorState* state) {
    if (DC_DEBUG == 1) {
        Serial.println("Receiving data ...");
        Serial.print("Current state: ");
        Serial.println(state->state);
    }
    if (state->state != STATE_NORMAL) {
        return;
    }
    uint32_t code = 0;
    uint8_t bytes = (bits + 7) / 8;
    for (int i = 0; i < bytes; i++) {
        code = code << 8;
        code = code | data[i];
    }
    state->cardCode = code;
    state->state = STATE_COMPARING;
    if (DC_DEBUG == 1) {
        Serial.print("Moving to state: ");
        Serial.println(state->state);
    }
}

void receivedDataError(Wiegand::DataError error, uint8_t* rawData, uint8_t rawBits, const char* message) {
    Serial.print(message);
    Serial.print(Wiegand::DataErrorStr(error));
    Serial.print(" - Raw data: ");
    Serial.print(rawBits);
    Serial.print("bits / ");

    uint8_t bytes = (rawBits + 7) / 8;
    for (int i = 0; i < bytes; i++) {
        Serial.print(rawData[i] >> 4, 16);
        Serial.print(rawData[i] & 0xF, 16);
    }
    Serial.println();
}

void networkEvent(arduino_event_id_t event) {
    int resultCode;
    switch(event) {
        case ARDUINO_EVENT_ETH_START:
            Serial.println("ETH Started");
            ETH.setHostname(DC_HOST_NAME);
            break;
        case ARDUINO_EVENT_ETH_CONNECTED:
            Serial.println("ETH connected");
            break;
        case ARDUINO_EVENT_ETH_GOT_IP:
            hasIp = true;
            Serial.print("ETH MAC: ");
            Serial.print(ETH.macAddress());
            Serial.print(", IPv4: ");
            Serial.print(ETH.localIP());
            if (ETH.fullDuplex()) {
                Serial.print(", FULL_DUPLEX");
            }
            Serial.print(", ");
            Serial.print(ETH.linkSpeed());
            Serial.println("Mbps");

            setClock(NULL);

            mqttClient.setServer(DC_MQTT_HOST, 1883);
            connectToMqtt();
            break;
        case ARDUINO_EVENT_ETH_DISCONNECTED:
            Serial.println("ETH Disconnected");
            hasIp = false;
            break;
        case ARDUINO_EVENT_ETH_STOP:
            Serial.println("ETH Stopped");
            hasIp = false;
            break;
        default:
            Serial.print("Got unhandled event");
            Serial.println(event);
            break;
    }
}

void setClock(void *_p) {
    configTime(0, 0, DC_NTP_HOST);

    Serial.print("Waiting for NTP time sync: ");
    time_t nowSecs = time(nullptr);
    while (nowSecs < 8 * 3600 * 2) {
        delay(100);
        yield();
        nowSecs = time(nullptr);
    }

    struct tm timeinfo;
    gmtime_r(&nowSecs, &timeinfo);
    Serial.print("Current time: ");
    Serial.println(asctime(&timeinfo));
    char payload[100];
    snprintf(payload, 100, "%s", asctime(&timeinfo));
    mqttClient.publish(TOPIC_LOG_INFO, 1, false, payload);
}

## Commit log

2024-01-14 add pcb design files
    [door-controller.kicad_pcb, door-controller.kicad_sch]
2024-07-27 Rename file so that arduino-cli stops complaining
2024-07-27 MQTT Proof of concept
    The goals where to be able to send logs, unlock/deny, and health check
    events to a MQTT broker. Also being able process a new card list by
    subscribing to the access_list topic. This allows for updating the
    cards.txt file without having to plug a laptop into the door controller.
    This change also includes all the plumbing for setting up the ETH
    connection and getting the MQTT broker IP using a DNS lookup.
    It also provides a way to change the default configuration.
    This is a POC which means it's not quite ready for prime time. It is
    however ready for more real world testing.
    [M2C_Yet_Another_Door_Controller.ino]
2024-07-27 Configurable NTP host and more logging
    Make NTP host a build argument.
    Add better logging over mqtt by using more descriptive topics.
    Add more logging of information to help debug any issues.
    Add code to throw out multipart payloads as we don't have the ability to
    handle those kinds of payloads at the moment.
    [M2C_Yet_Another_Door_Controller.ino]
2024-07-27 Testing out reseting NTP
    [M2C_Yet_Another_Door_Controller.ino]
2024-07-27 Finished Testing Door Controller
    - Updated the code base to use arduino-esp32 version 3.0.2
    - Change MQTT from the async to secure client so that it would be
    possible to connect to the MQTT server using TLS
    - Added root_ca.h header
    - Changed MQTT client timeout from 2 to 5 seconds
    - Fixed snprintf string formatting issues
    - Removed DNS check since the MQTT client setServer function can accept
    a string which is needed for TLS anyways
    - Cleaned up the main loop
    - Updated README.md for better example and more information. Still a WIP
    [M2C_Yet_Another_Door_Controller.ino]
2024-08-06 Fixed issues with card list file
    - Removed the line adding EOF to the end of the file. This is not needed
    and results in a 0xFF being inserted at the end of the file which
    causes some issues if the last code isn't followed by a new line.
    - Refactored a few variable names to help with readability
    - Added in more debug print statements
    - Changed the code that takes the payload and copies it to the card list
    file. The previous approach was overly complex for no reason. The new
    code is a lot simpler and easier to understand what's going on.
    [M2C_Yet_Another_Door_Controller.ino]
